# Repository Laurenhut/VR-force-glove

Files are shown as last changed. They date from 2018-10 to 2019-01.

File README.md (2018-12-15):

VR Force glove
====
This is the repository for a locking vr force glove. This readme will go over how to assemble and run the software needed to make the glove work. To find more information on the design an build process see the post made on my portfolio made [here]()
***

setup and use guide
=======
 parts needed
---
* 3d printer
* arduino nano
* load cell
* hobbyist servo motor
* 1/4 drive hand ratchet
* blue smirf silver Bluetooth module
* potentiometor
* m2 and m5 screws
* at least 3in long guide rail and 17mm Ball bearing carriage
* 20 gauge galvanized steel wire or 3in control rod

assembling the glove
---

1. print the stl files located in the stl folder
2. slip the 1/4 drive hand ratchet into the opening of the index_attachment and push the ratchet head into the corresponding opening on the side of the body piece

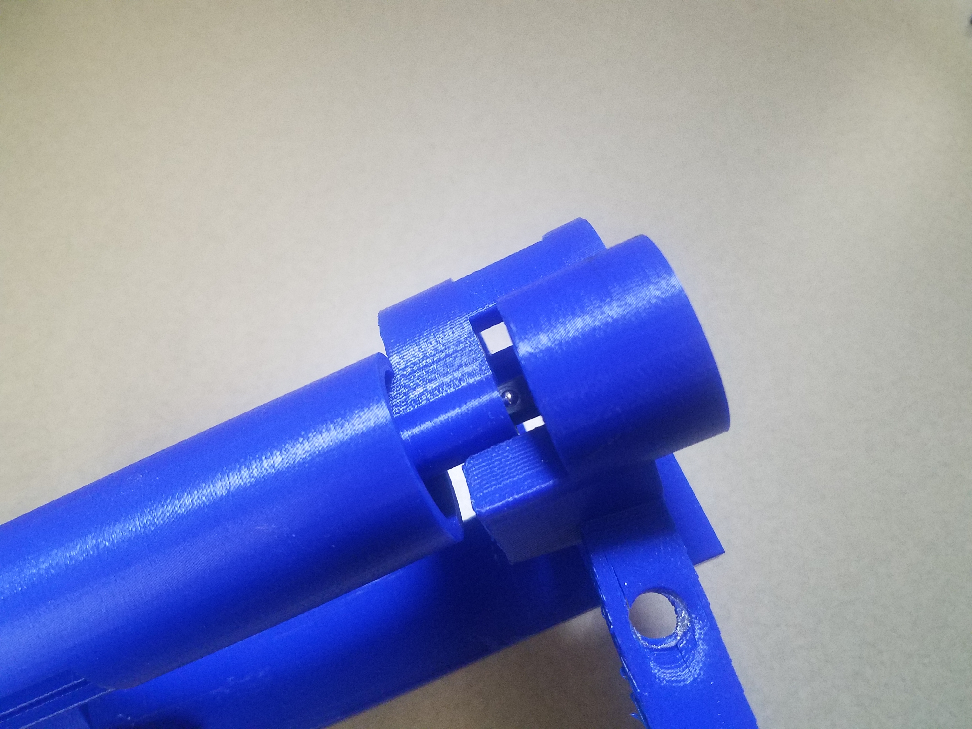
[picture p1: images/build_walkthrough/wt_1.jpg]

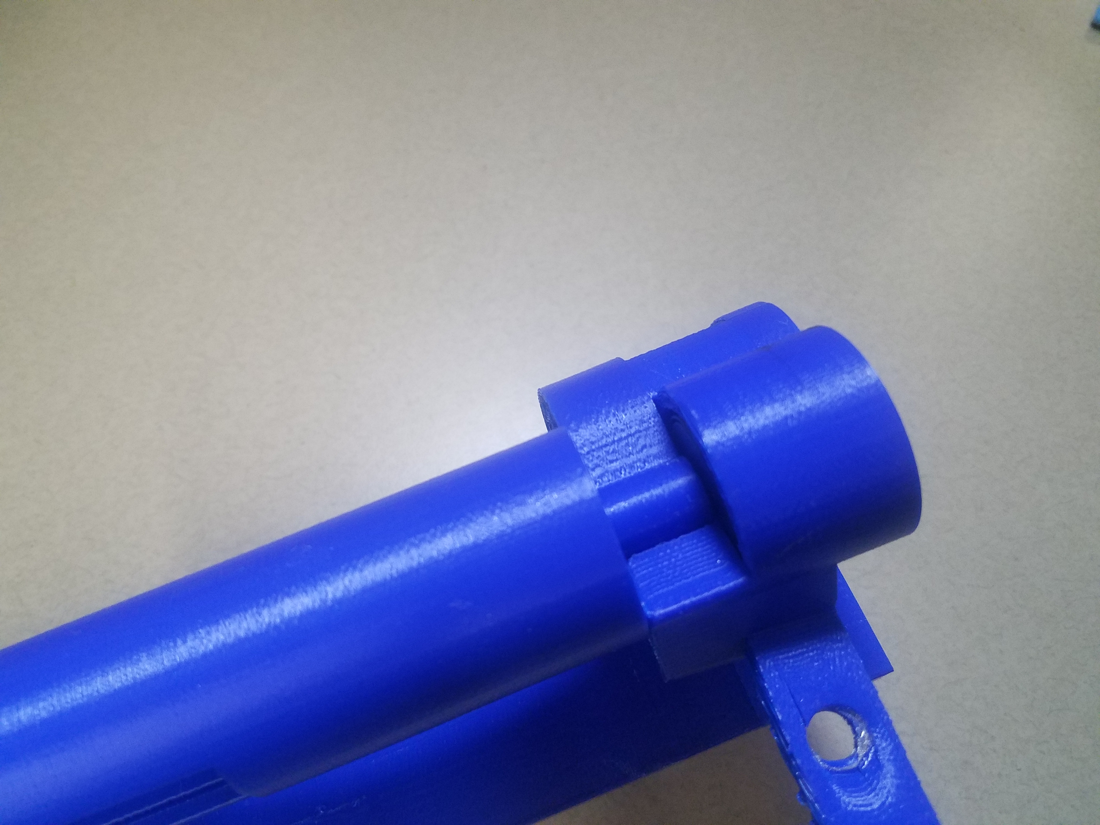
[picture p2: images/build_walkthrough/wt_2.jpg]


3. place the control_lever over the ratchet head and make sure that the lever is facing upwards and can swing clockwise
  - if the ratchet is in the incorrect orientation return to step 3 and reorient it

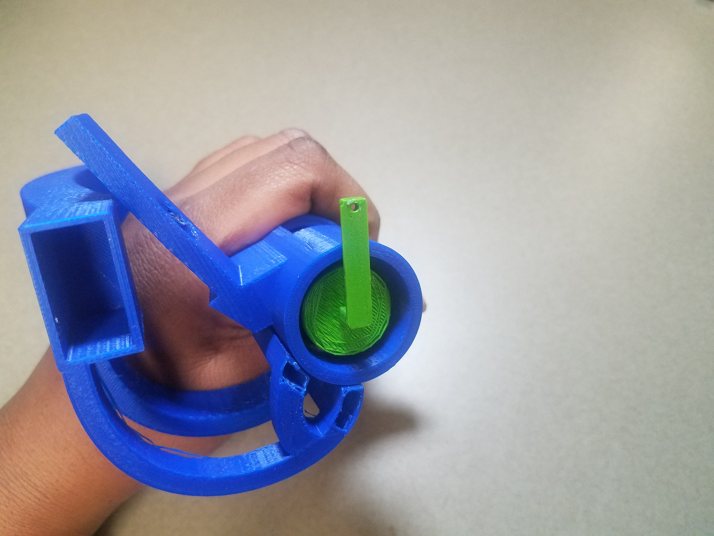
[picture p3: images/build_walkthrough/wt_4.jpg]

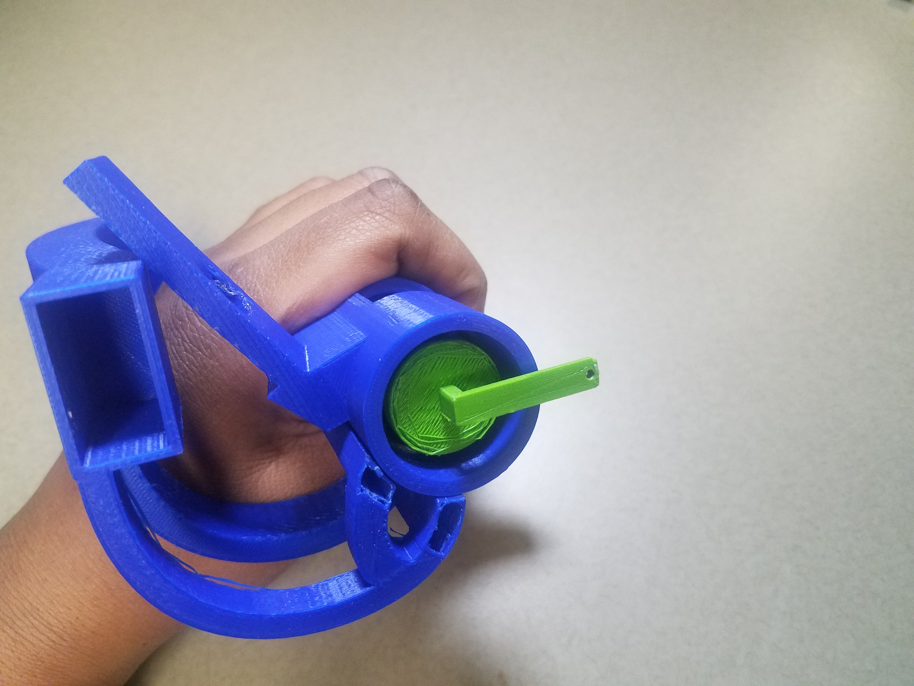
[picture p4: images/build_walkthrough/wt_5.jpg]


4. put the control_lever through the center hole of the ratchet_cap
5. place the potentiometor into the pot_casing piece and put the knob of the potentiometor into the ratchet_cap piece
6. slide the pot_casing price into its slots on the handle piece as well as sliding the ratchet_cap over the ratchet
7. make sure that the control_lever is able to flick the locking direction of the ratchet when the cap on top
8. place a small piece of glue or tape onto the ratchet_cap to lock it into place on the ratchet_case

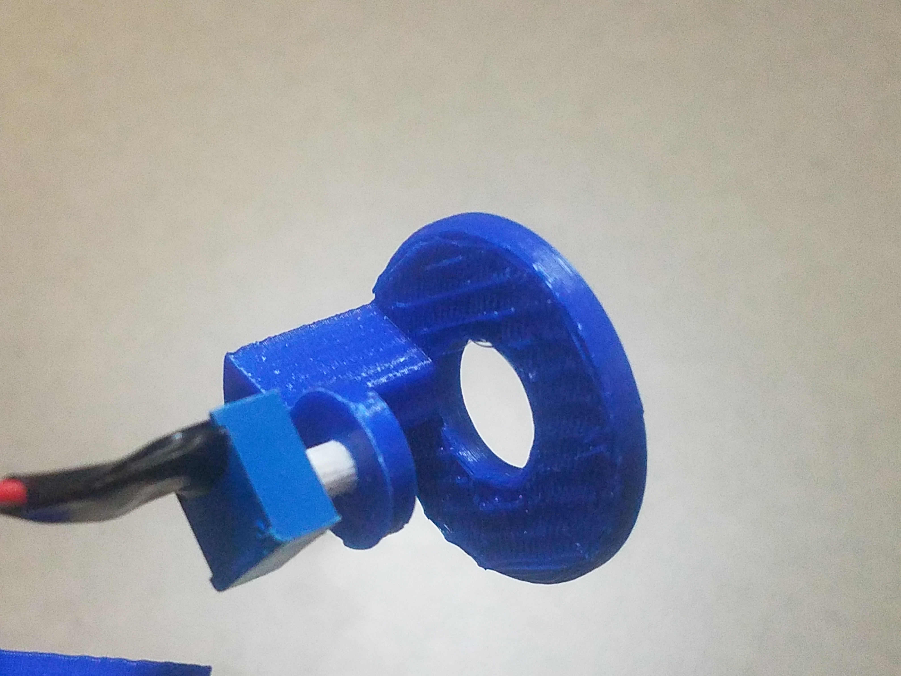
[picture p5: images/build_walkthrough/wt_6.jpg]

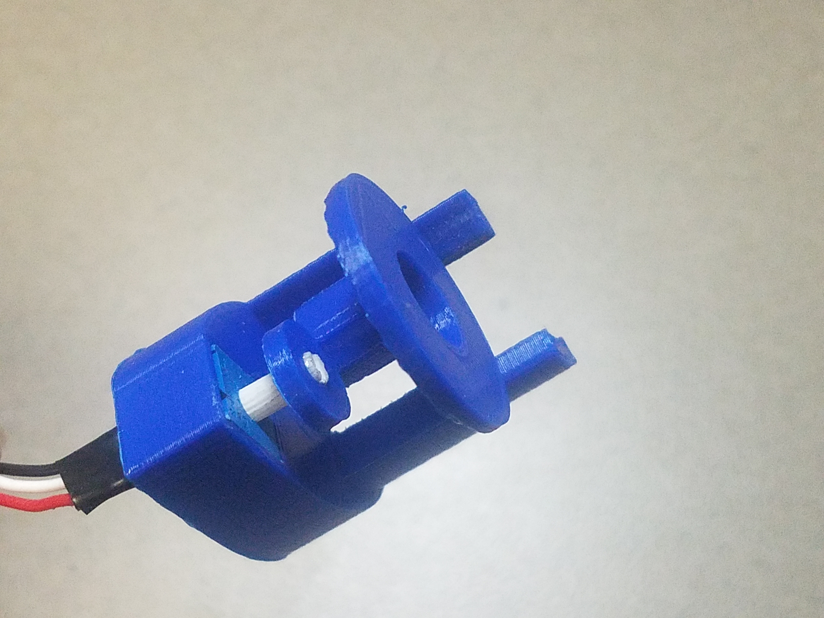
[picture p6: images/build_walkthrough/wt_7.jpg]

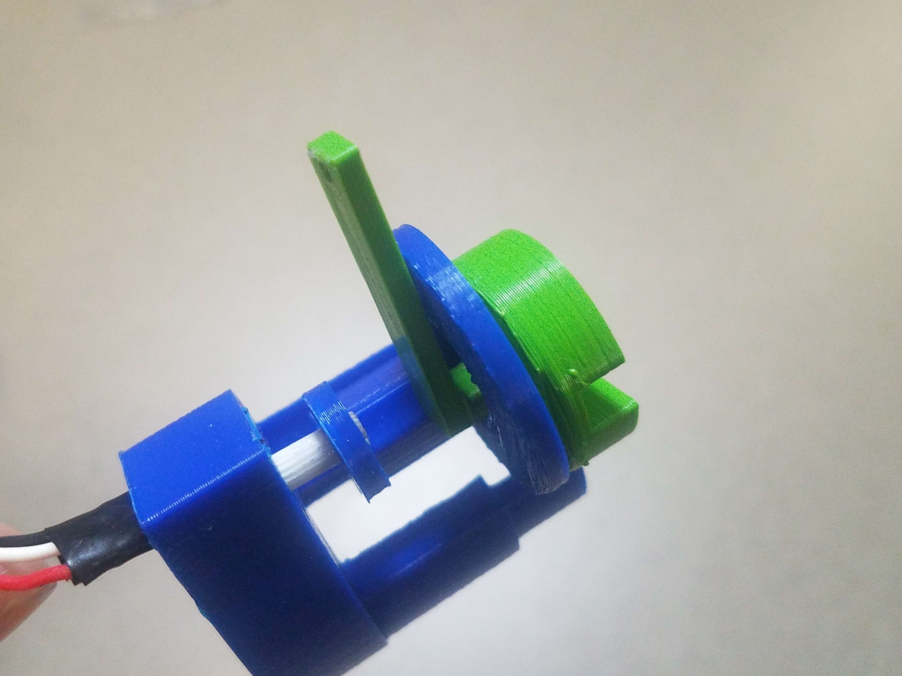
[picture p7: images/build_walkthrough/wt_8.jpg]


9. create a 3 inch push rod using the steel wire
10. slide the push rod into the hole on the end of the control_lever and the hole on the end of the hobby servo horn.
11. place the hobby servo into its casing at the end of the

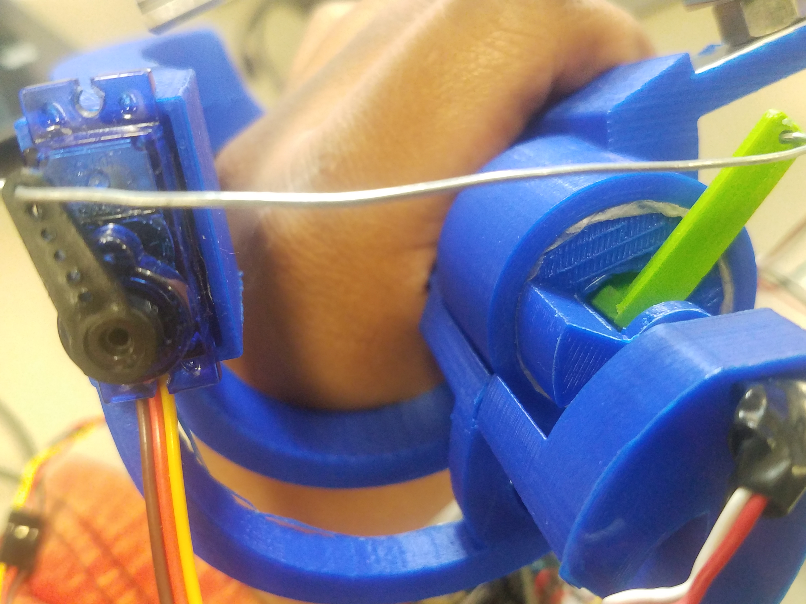
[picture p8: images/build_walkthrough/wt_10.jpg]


12. slide the bottom half of the strain gauge into the thumb piece as shown. And tighten the bottom bolt.
13. Screw on the rest of the strain gauge

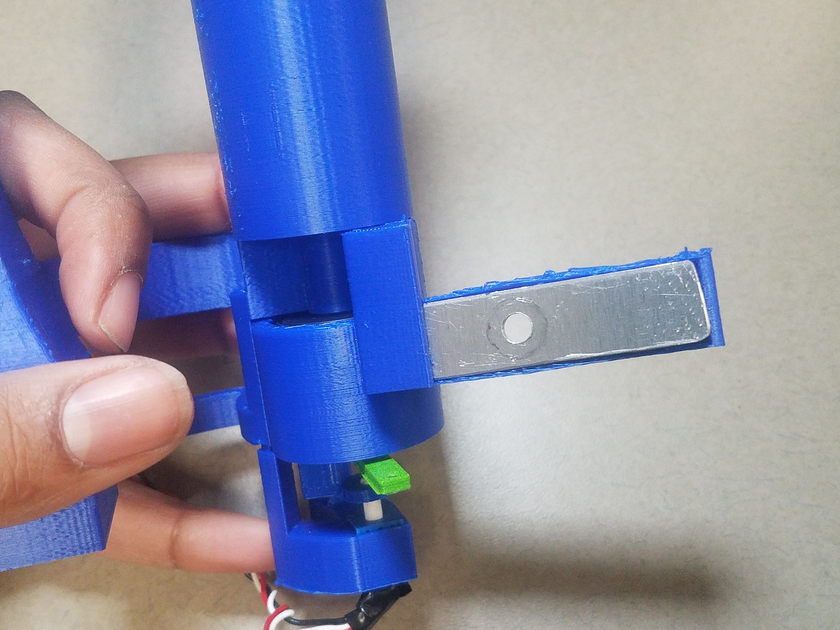
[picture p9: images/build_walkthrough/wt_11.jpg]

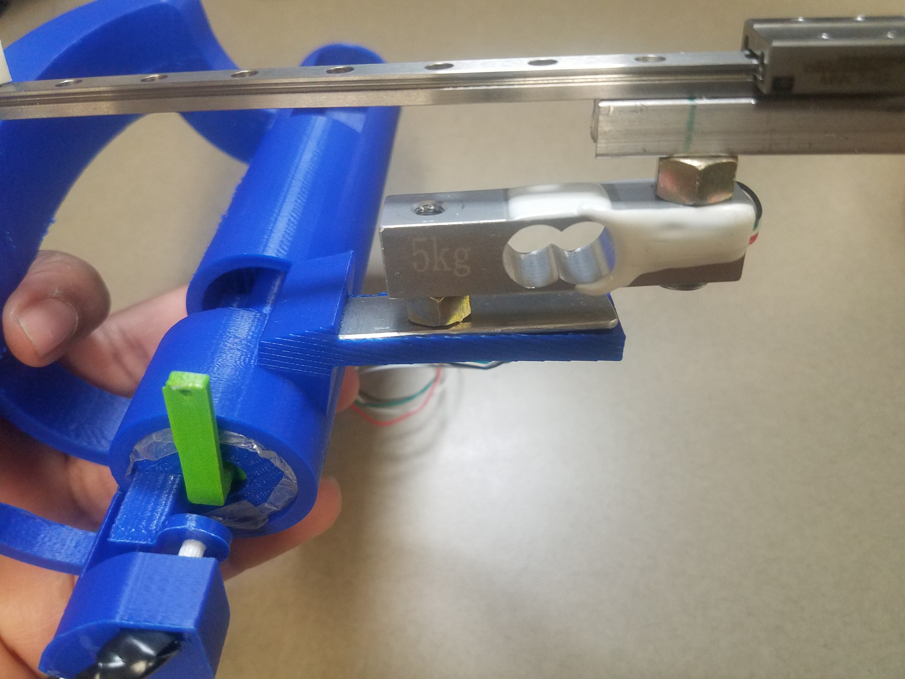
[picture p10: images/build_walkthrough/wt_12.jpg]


14. place the index_ring_adapter over the linear slide carriage and attach using m2 screws
15. test to make sure the index_ring_adapter and slide are working correctly
  - note: you may have to angle the linear slide slightly to make finger actuation more comfortable
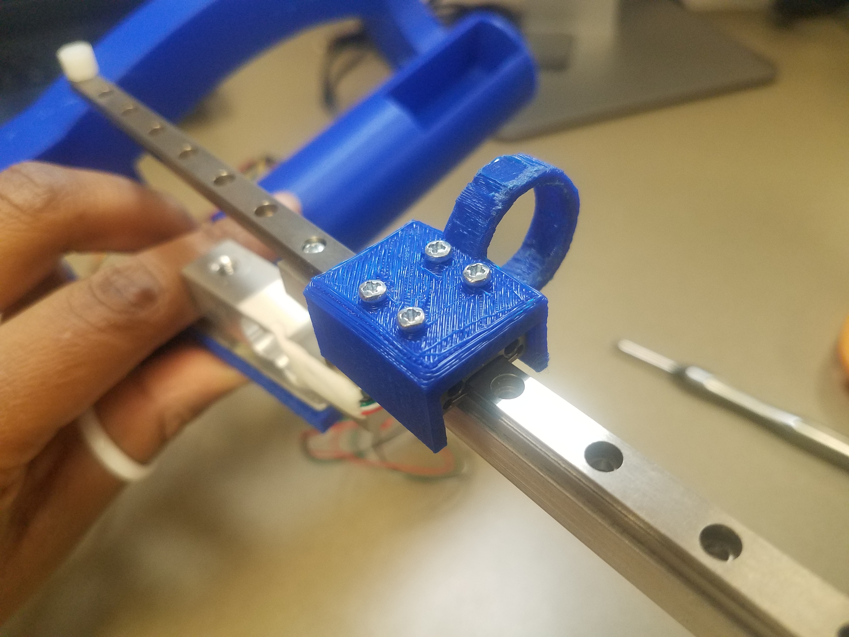
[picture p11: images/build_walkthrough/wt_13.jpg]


16. screw the puck_mount onto the Vive puck
17. place the puck_mount onto the back of the handle
18. slide the stabilization rods into the holes of the puck_mount.

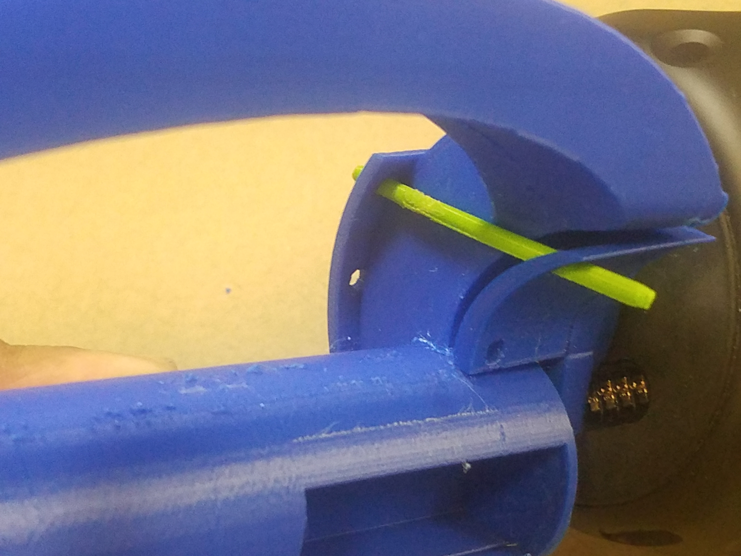
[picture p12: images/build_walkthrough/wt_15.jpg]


Running the software
---
1. assemble the circuit shown in the circuit folder
2. upload the " bluetooth_with_imu" sketch to the Arduino nano and open the serial monitor
3. follow the steps for calibration
  - note: the bottom number should be smaller than the top number. If these values are reversed check your potentiometor
4. pair your blue smirf with your windows computer
5. start Steam VR, and make sure your Vive is properly setup and the vive puck is paired
6. open up the unity project
7. run the python script "virtual_joystick_windows.py"
  - note: in Steam VR a game pad controller icon should appear
8. run the unity project
9. the device should be working now grab something and test it

Package references
---
T. (n.d.). NewtonVR. Retrieved from https://github.com/TomorrowTodayLabs/NewtonVR

B. (n.d.). PYXInput. Retrieved from https://github.com/bayangan1991/PYXInput

M. (n.d.). Pywn32. Retrieved from https://github.com/mhammond/pywin32

V. (n.d.). Steamvr_unity_plugin. Retrieved from https://github.com/ValveSoftware/steamvr_unity_plugin/tree/master/Assets/SteamVR

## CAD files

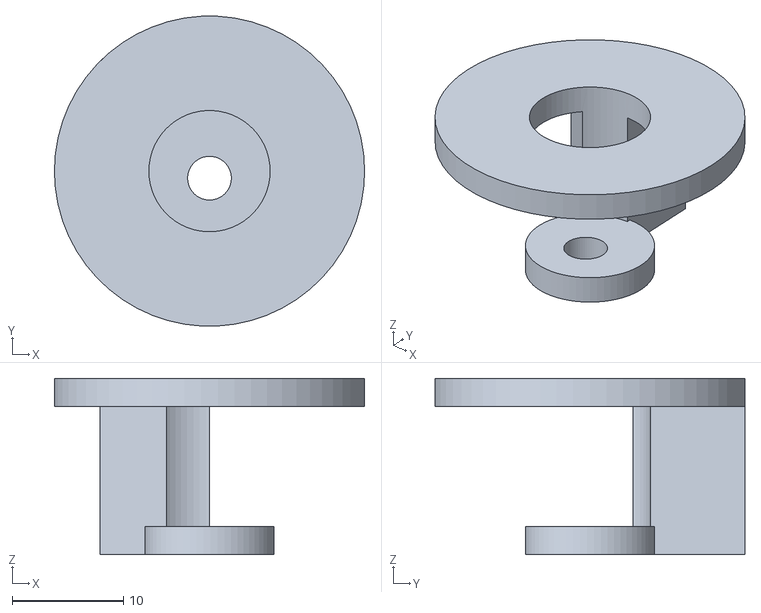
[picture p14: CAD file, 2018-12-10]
stl_files/ratchet_cap.stl
27.9 x 27.9 x 15.9

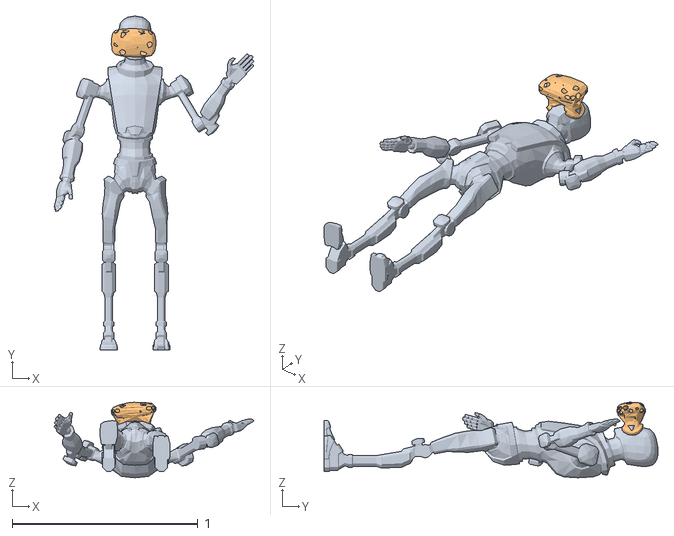
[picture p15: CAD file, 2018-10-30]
unity/Lauren's Env/Assets/NewtonVR/Meshs/NVREditorPlayer.obj
1.08 x 1.80 x 0.408
Robot2_Untitled
Headset_Plane006.001

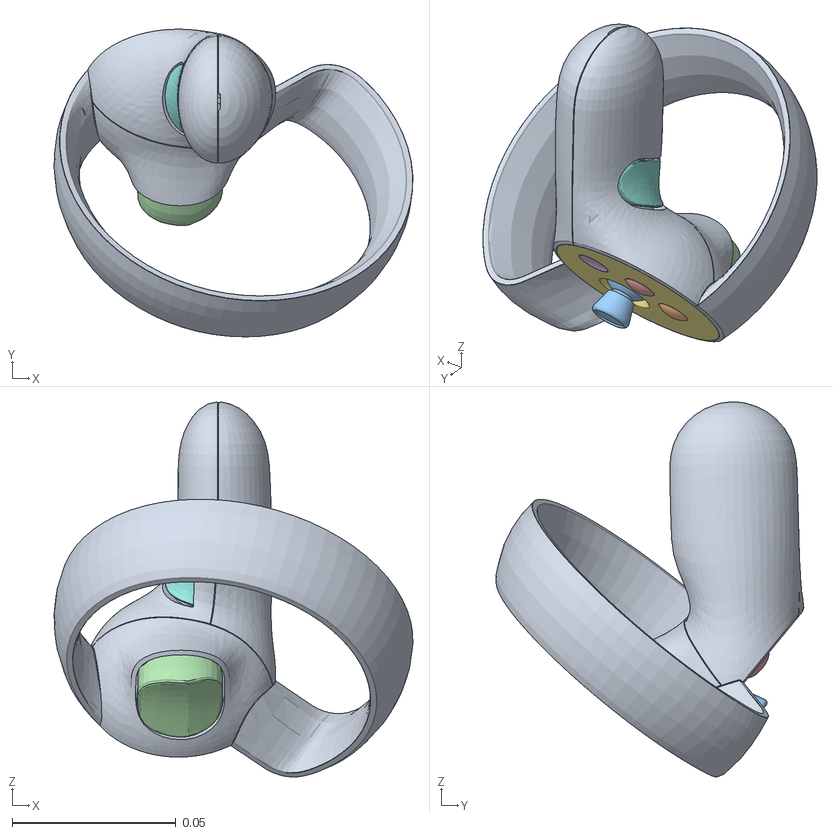
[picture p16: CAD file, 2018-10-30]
unity/Lauren's Env/Assets/NewtonVR/Resources/TouchControllers/oculusTouchRightModel.obj
0.11 x 0.0941 x 0.115
tooche_group4_body
tooche_group4_control_surface_group2_button1
tooche_group4_control_surface_group2_thumb_stick
tooche_group4_trigger
tooche_group4_control_surface_group2_button2
tooche_group4_control_surface_group2_button3
tooche_group4_face_control_surface_group2
grip_tooche_group4

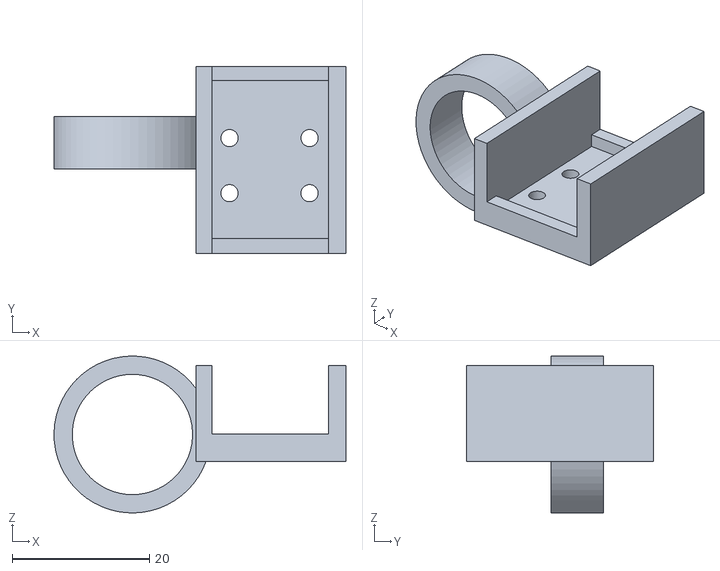
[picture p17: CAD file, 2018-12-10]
stl_files/index_ring_adapter.stl
42.5 x 27.3 x 22.8

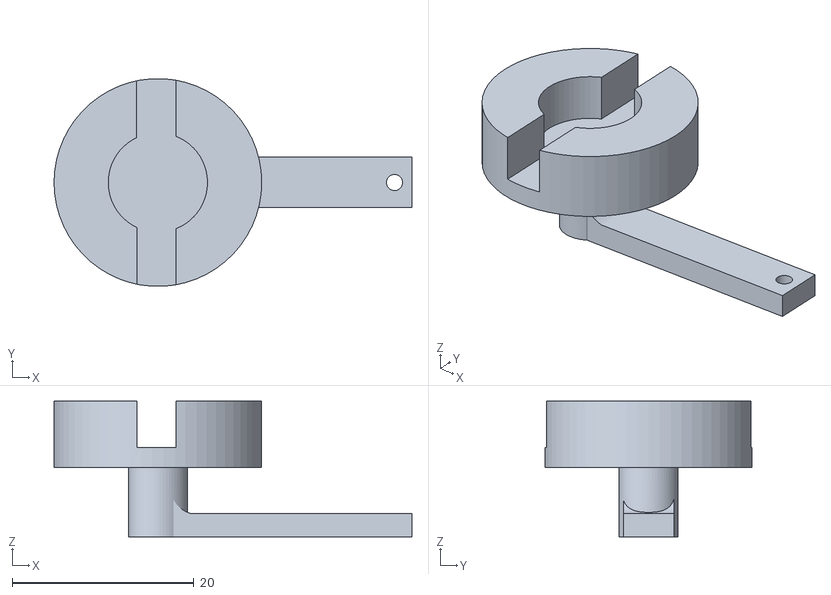
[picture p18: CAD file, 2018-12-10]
stl_files/control_lever.stl
39.4 x 22.8 x 14.9

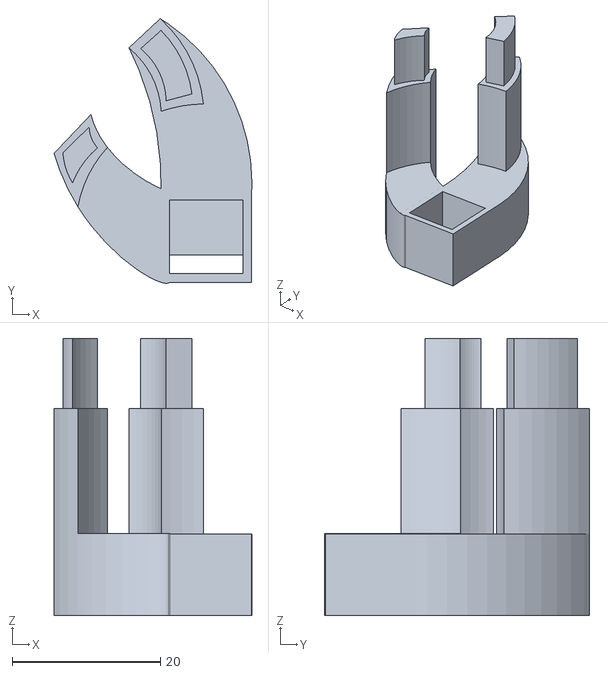
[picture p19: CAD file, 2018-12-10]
stl_files/pot_case.stl
26.7 x 35.7 x 37.4

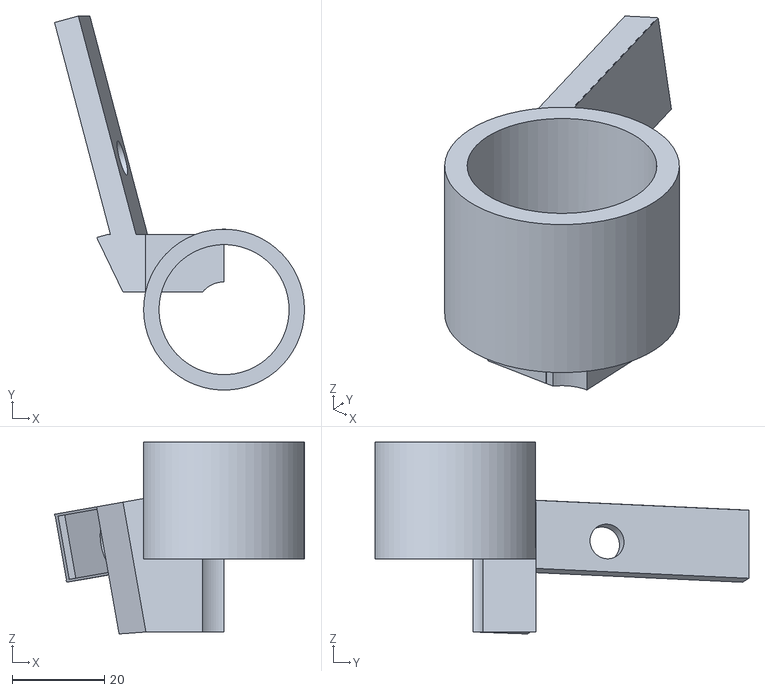
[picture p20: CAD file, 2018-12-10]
stl_files/index_attachment.stl
54.2 x 81.1 x 41.6

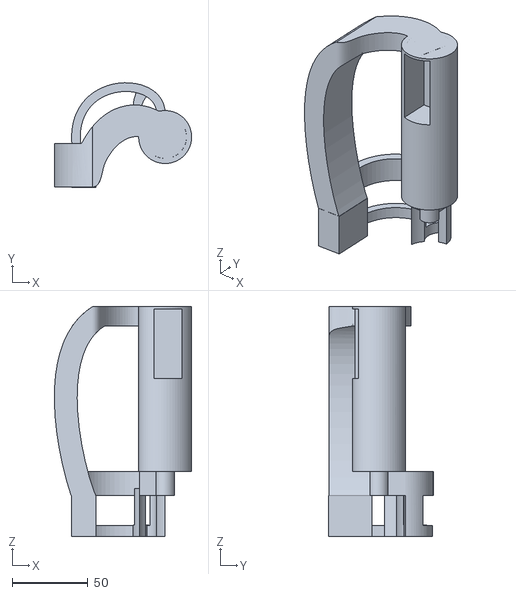
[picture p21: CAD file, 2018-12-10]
stl_files/Handle.stl
90.4 x 68.8 x 151.3

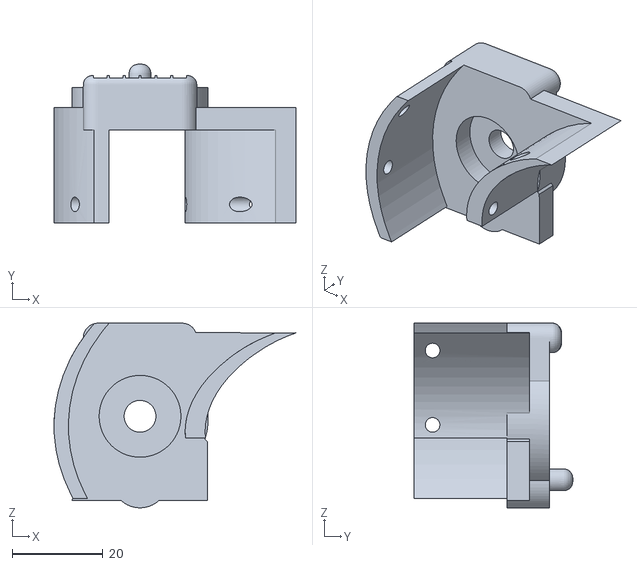
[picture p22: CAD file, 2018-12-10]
stl_files/puck_mount.stl
53.3 x 34.9 x 40.7

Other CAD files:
unity/Lauren's Env/Assets/NewtonVR/Resources/TouchControllers/oculusTouchLeftModel.obj
unity/Lauren's Env/Assets/chair.blend

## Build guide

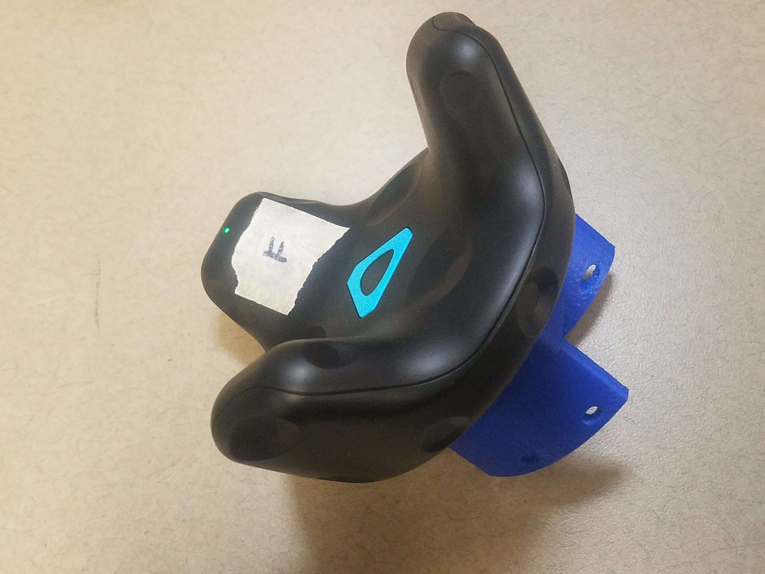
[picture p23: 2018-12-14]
images/build_walkthrough/wt_14.jpg

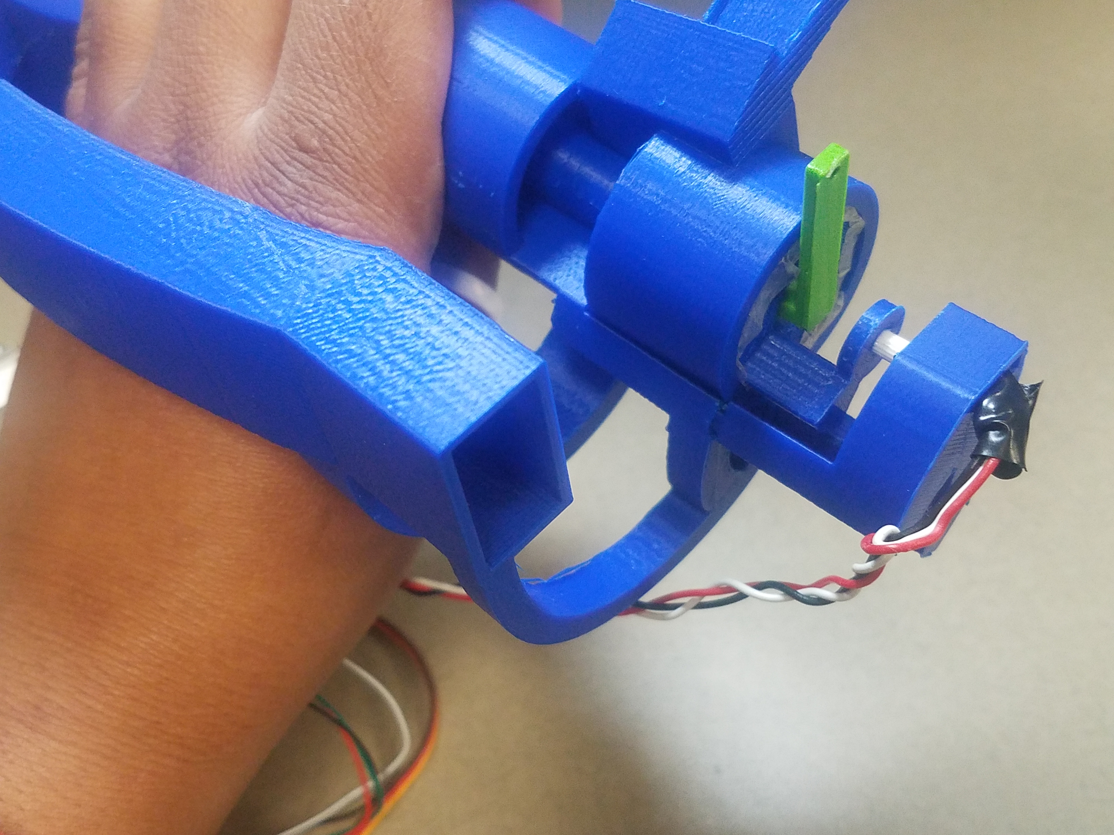
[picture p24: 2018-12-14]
images/build_walkthrough/wt_9.jpg

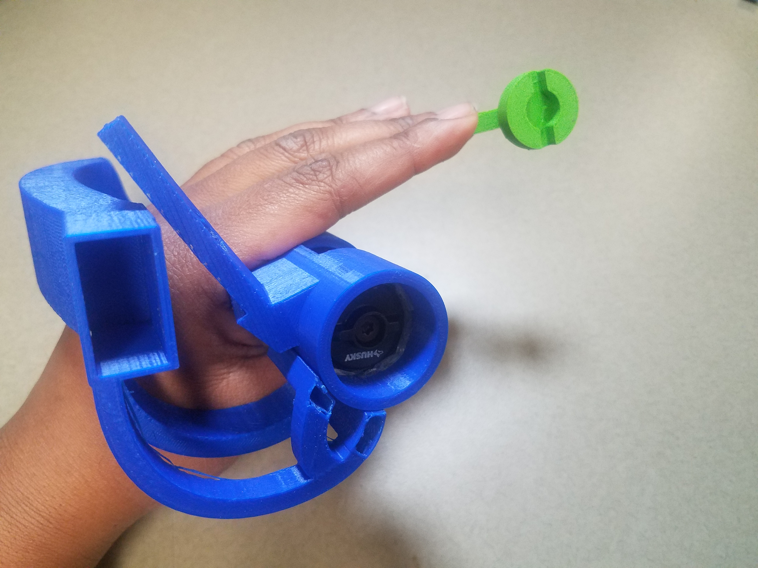
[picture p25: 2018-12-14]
images/build_walkthrough/wt_3.jpg

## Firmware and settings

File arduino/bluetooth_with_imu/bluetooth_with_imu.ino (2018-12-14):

/*

 Hardware setup:
 pot --------- Arduino
 VDD ---------------------- 3.3V
 VDDI --------------------- 3.3V
 SDA ----------------------- A4
 SCL ----------------------- A5
 GND ---------------------- GND

 Bluetooth 
 Motor 
 
 */
#include "HX711.h"

#define DOUT  4
#define CLK  5

HX711 scale(DOUT, CLK);

float calibration_factor = -1958240; //-7050 worked for my 440lb max scale setup-208240

#include <SoftwareSerial.h>
#include <PWMServo.h>
PWMServo myservo;  // create servo object to control a servo
// potentiometor 
int potPin = 2;

// variable to store the servo position
int pos = 0;    

// bluetooth pins
int bluetoothTx = 2;  // TX-O pin of bluetooth mate, Arduino D2
int bluetoothRx = 3;  // RX-I pin of bluetooth mate, Arduino D3
int blue = 0;
float value = 0.5;

SoftwareSerial bluetooth(bluetoothTx, bluetoothRx);


void setup()
{
  myservo.attach(SERVO_PIN_A);  // attaches the servo on pin 9 to the servo object
  myservo.write(105);
 
  Serial.begin(9600);

  // setsup bluetooth communications
  bluetooth.begin(115200);  // The Bluetooth Mate defaults to 115200bps
  bluetooth.print("$");  // Print three times individually
  bluetooth.print("$");
  bluetooth.print("$");  // Enter command mode
  delay(100);  // Short delay, wait for the Mate to send back CMD
  bluetooth.println("U,9600,N");  // Temporarily Change the baudrate to 9600, no parity
  bluetooth.begin(9600);  // Start bluetooth serial at 9600

  // activates strain gague and resets it to zero
  scale.set_scale();
  scale.tare(); 
  
  //Get a baseline reading
  long zero_factor = scale.read_average();
  myservo.write(105);
}

//checks the force on the force sensor and returns the result
float force_sensor_value(){
        scale.set_scale(calibration_factor); //Adjust to this calibration factor
        float  force_value= scale.get_units();
      Serial.print("ff"); 
      Serial.println(force_value);
        return force_value; 
}

// read the value from the sensor
float pot_data()
{
    float val = analogRead(potPin);

    return val;
  }

void  change_motor(int current_position)
{
     //locked position
     if (current_position == true)
     {
        myservo.write(180);
      }
      // freewheeling position
     else
     {
        myservo.write(105);

      }

  }

struct Data
  {
    int bottom, top; 
    float locked_force,squeeze_force;
  };

struct Data calibrate()
  {
    int var =0;
    int var2 = 0; 
    int bottom, top; 
    float locked_force, squeeze_force; 
     
    Serial.println("calibrating hold at bottom for 5s");
           delay(5000); 
  
    bottom = pot_data();  
  
    Serial.println("calibrating hold at top for 5s");
    delay(5000); 
    
    top = pot_data(); 
    Serial.println("place finger in the middle");
    delay(5000);
    
    Serial.println("locking device, relax fingers");
    myservo.write(180);
    delay(5000);
    locked_force = force_sensor_value(); 
    
    Serial.println("squeeze device");
    delay(5000);
    squeeze_force = force_sensor_value(); 

    Serial.println("unlocking device");
    myservo.write(105);
    
    Serial.println("done calibrating");
    return {bottom, top,locked_force,squeeze_force};
  }

bool glove_locked = false;
float frozen_position; 
struct Data cal;
bool start = true; 
float position_pot; 

void loop()
{
    if (start == true){  
      cal =calibrate();   
      Serial.println(cal.bottom); 
      Serial.println(cal.top);  
      Serial.println(cal.locked_force); 
      Serial.println(cal.squeeze_force); 
      start =false; 
    }
   
  // checks if the bluetooth sent signal to lock the glove
    if(bluetooth.available())  // If ths bluetooth sent any characters
  {
    // prints out the values sent by the bluetooth module
    blue = bluetooth.read();
    Serial.println(char(blue));
    
    if(char(blue) == "1")
      {
        Serial.println("locking: ");
        glove_locked = true; 
  
      }
    else if (char(blue)== "0")
      {
        Serial.println("unlocking ");
        glove_locked = false; 
      }

    else
      {
         switch (glove_locked) 
         {
          case true:
            Serial.println("unlocking ");
            glove_locked = false;
            break;
          case false: 
            Serial.println("locking ");
            glove_locked = true;
            break;
          }
    
      }

    change_motor(glove_locked);

       //sends command to lock the glove locks the glove
  }


   //locks the position of the fingers and will not update it until the force sensor reads correctly 
  if (glove_locked == true)
    {
      float finger_force = force_sensor_value();
      if (finger_force >(cal.locked_force+.03))
        {
          bluetooth.println(frozen_position);
          Serial.print("pos frozen: ");
          Serial.print(frozen_position);
          Serial.print(" force: ");
          Serial.println(finger_force);
        }
      // if your not puhing on the force sensor then it will begin updating as normal
      else if (finger_force <(cal.locked_force+.03) )
        {
          position_pot= (pot_data()-cal.bottom)/(cal.top-cal.bottom);
          Serial.print("pos locked: ");
          Serial.println(position_pot);
          bluetooth.println(position_pot);
        }

    }
   //sends the position of the fingers through bluetooth as freewheeling
   else
   {
        position_pot= (pot_data()-cal.bottom)/(cal.top-cal.bottom);
        bluetooth.println(position_pot);
    }
   frozen_position =  position_pot; 
   delay(50);

}

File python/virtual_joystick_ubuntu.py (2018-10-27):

import uinput
import time
def main():
    # the bluetoothe module will feed into this controller script
    # this controller script will then
    #useful commands  evtest
    #usefull command #2 sudo jstest /dev/input/js0
    events = (
        uinput.BTN_JOYSTICK, # maybe the force sensor values
        uinput.ABS_X+(0, 0, 0, 0), # accelerometor values
        uinput.ABS_Y + (0, 0, 0, 0),
        )
    x_axis = 0
    y_axis = 0
    ans= "g"
    with uinput.Device(events) as device:
        while ans != "e":
            ans = raw_input("press a button: a, s, d, f ")
            print (ans)
            if ans == "a":
                while True:
                    x_axis-=1
                    device.emit(uinput.ABS_X,x_axis)
                    #the acceleromitor values will go here
                    time.sleep(0.01)
            elif ans == 'd':
                x_axis+=1
                device.emit(uinput.ABS_X, x_axis)
            elif ans =='w':
                y_axis+=1
                device.emit(uinput.ABS_Y, y_axis)
            elif ans =='s':
                y_axis-=1
                device.emit(uinput.ABS_Y, y_axis)
            elif ans =='e':
                print("end")


if __name__ == "__main__":
    main()

# import time
#
# import uinput
#
# def main():
#     events = (
#         uinput.REL_X,
#         uinput.REL_Y,
#         uinput.BTN_LEFT,
#         uinput.BTN_RIGHT,
#         )
#
#     with uinput.Device(events) as device:
#         for i in range(20):
#             # syn=False to emit an "atomic" (5, 5) event.
#             device.emit(uinput.REL_X, 5, syn=False)
#             device.emit(uinput.REL_Y, 5)
#
#             # Just for demonstration purposes: shows the motion. In real
#             # application, this is of course unnecessary.
#             time.sleep(0.01)
#
# if __name__ == "__main__":
#     main()

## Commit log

2018-10-24 added motor arduingo script working with button presses
2018-10-30 added unity files to github
    [NVREditorPlayer.obj, chair.blend, oculusTouchLeftModel.obj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]
2018-10-30 added line that will allow for data transfer from cpu to arduino
2018-10-31 connected arduino imu data to the virtual controller via the bluetooth serial communications. Connected the imu hardware and have acurate output values.
2018-11-01 added feedback from unity to python. added force sensor to the arduino.
2018-11-09 added calibration step for the imu and binds the imu values to be between 0 and 1. Added the motor lock/ unlock to the arduino code. Changed the servo library to pwm servo due to interfearance with t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
    [bluetooth_with_imu.ino, virtual_joystick_windows.py]
2018-11-13 locked the imu values to be between 1 and .75 to make a more realistic looking simulation
2018-11-19 updated arduno code to use the potentiometor and dded correct logic to deal with the force sensor
    [bluetooth_with_imu.ino]
2018-11-21 fixed bug that prevented the motor form locking correctly, arduino side
    [bluetooth_with_imu.ino]
2018-11-21 fixed bug that prevented motor from activating reliably on pyton side
    [virtual_joystick_windows.py]
2018-12-07 updated arduino file to use the strain gague
2018-12-08 arduino/unit tests/index_motor/index_motor.ino Please enter the commit message for yq#hanges. Lines starting
2018-12-10 added final stl files, made a README, added schematic diagram
    [Handle.stl, control_lever.stl, index_attachment.stl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]
2018-12-11 added updated motor ranges and the image folder
2018-12-12 added calibration step for force sensor, makes it so even if the values dirft a little bit the sensor will still be acurate
2018-12-14 added a detail about the guide rail
